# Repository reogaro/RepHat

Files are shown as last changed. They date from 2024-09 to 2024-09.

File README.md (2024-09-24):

# RepHat

"**R**epRap **E**xtension for **P**i"-**Hat**

Designed in Kicad. Open Source Hardware.

> [!CAUTION]
> This project is still in development and not ready for use!

A Raspberry Pi Hat for controlling stepper motors. Intended to be a [RAMPS](https://reprap.org/wiki/RAMPS_1.4) for the Raspberry Pi.

Built for use with LinuxCNC. See [here](https://github.com/reogaro/linuxcnc-pi4b-gpio) for some configuration examples.

## Features:

- 12-24 V Input Voltage
- 5V for Raspberry Pi with TI LMR51450 Switching Regulator
- Four Toshiba TB67S109AFTG Stepper Drivers
- Four endstop inputs with selectable voltages
- Input protection

## Current progress

[Schematic](output/schematic.pdf): Complete
[Routing](output/routing.pdf): Work in progress

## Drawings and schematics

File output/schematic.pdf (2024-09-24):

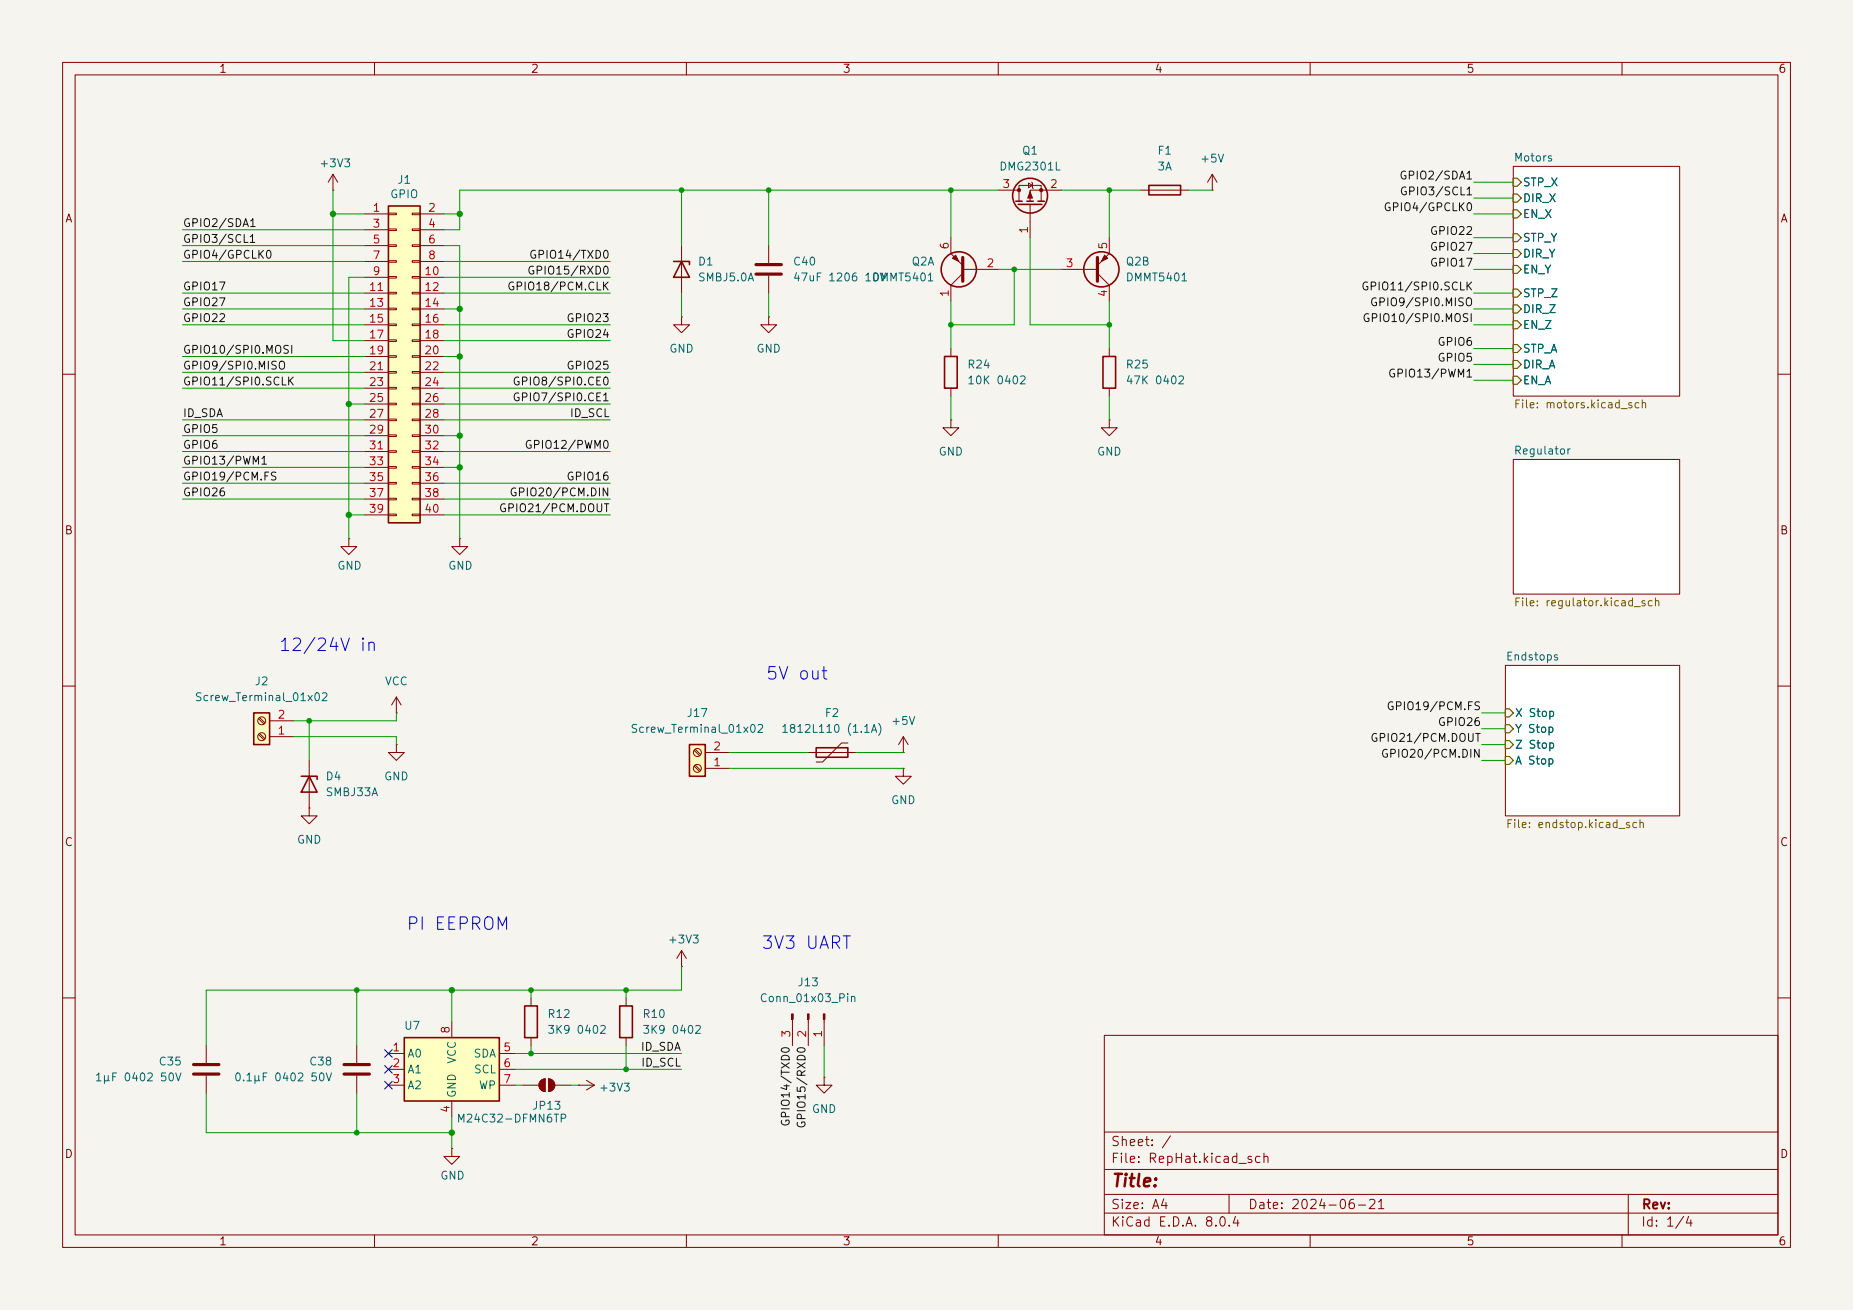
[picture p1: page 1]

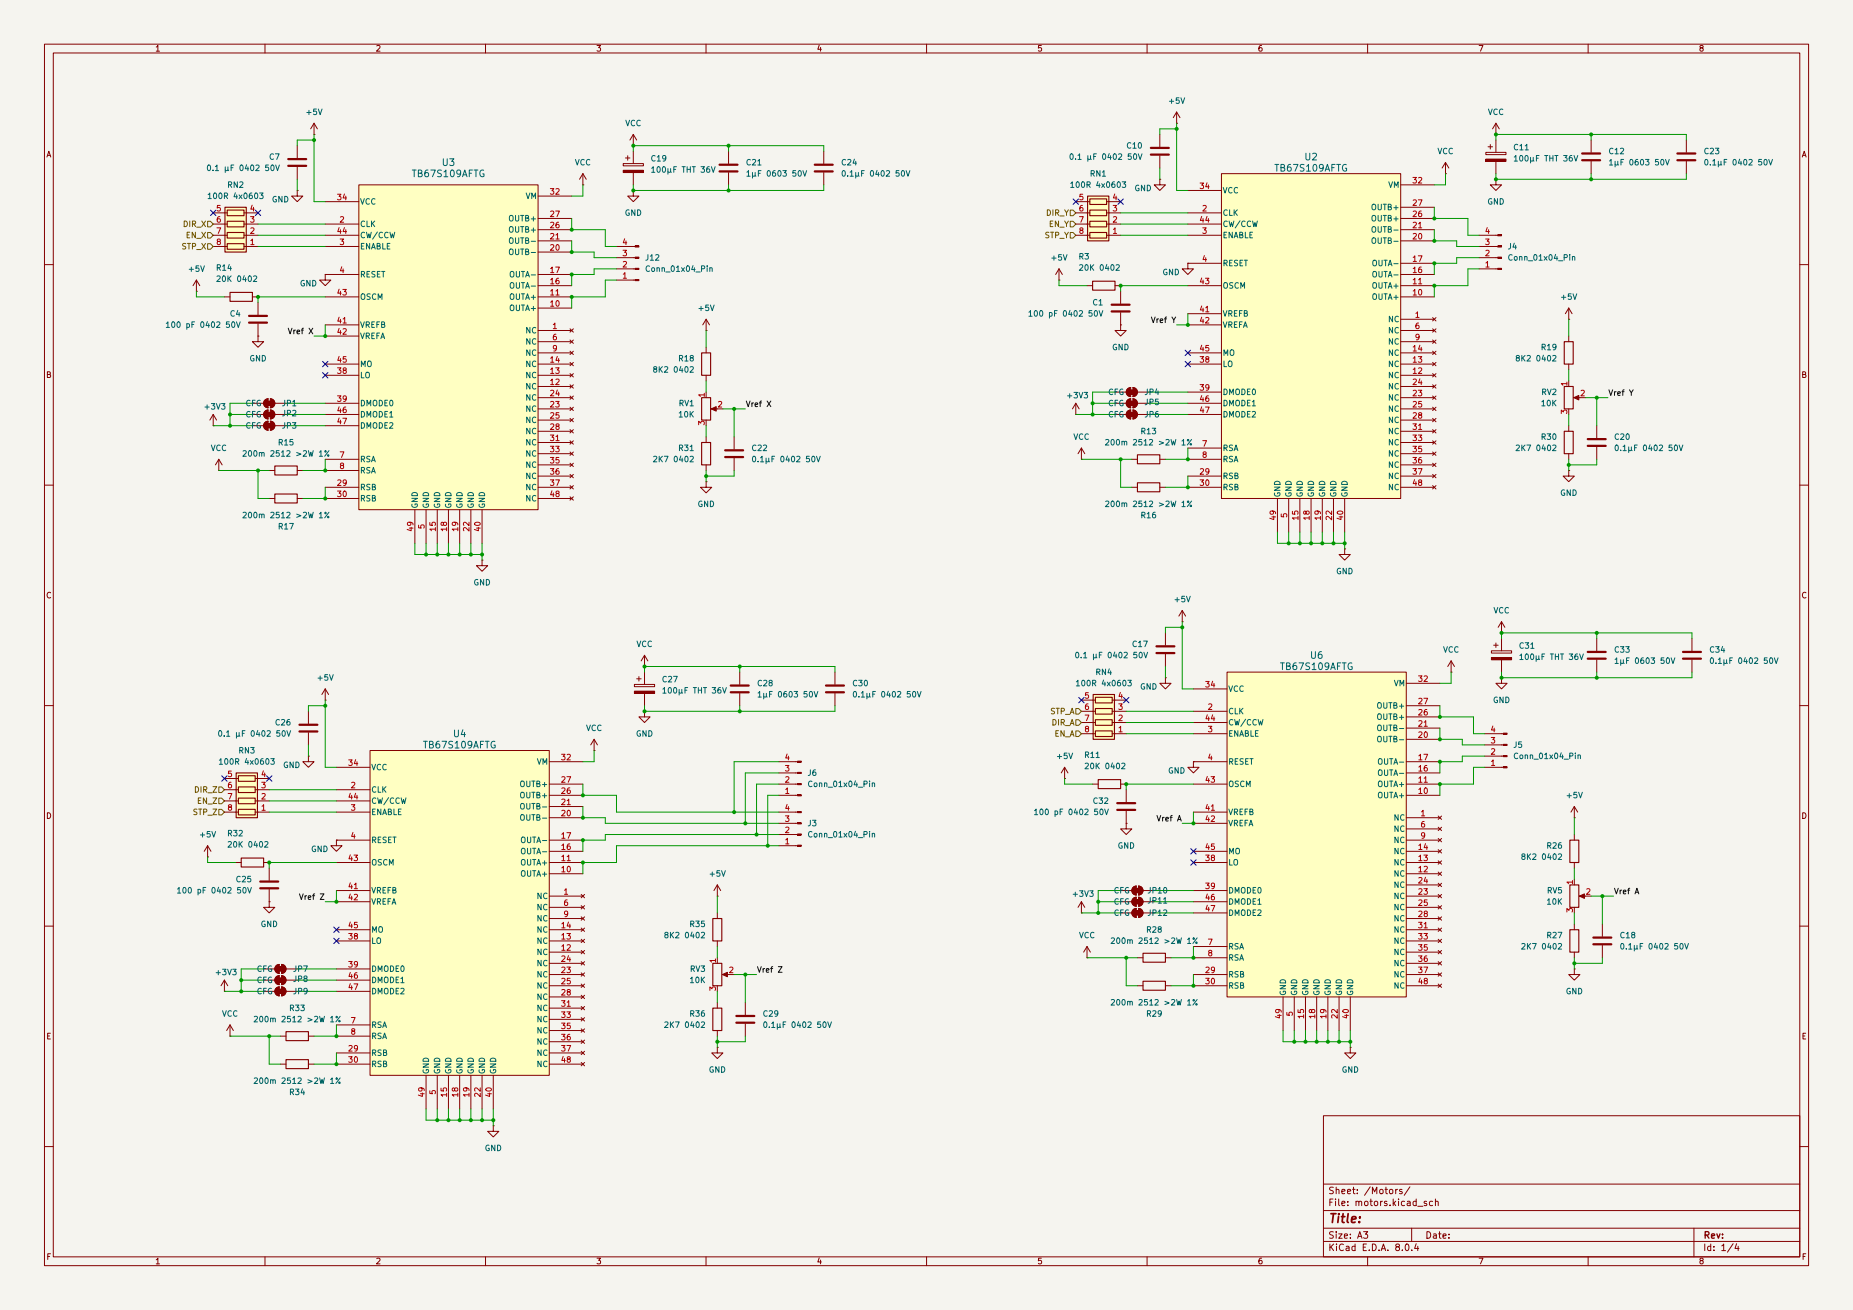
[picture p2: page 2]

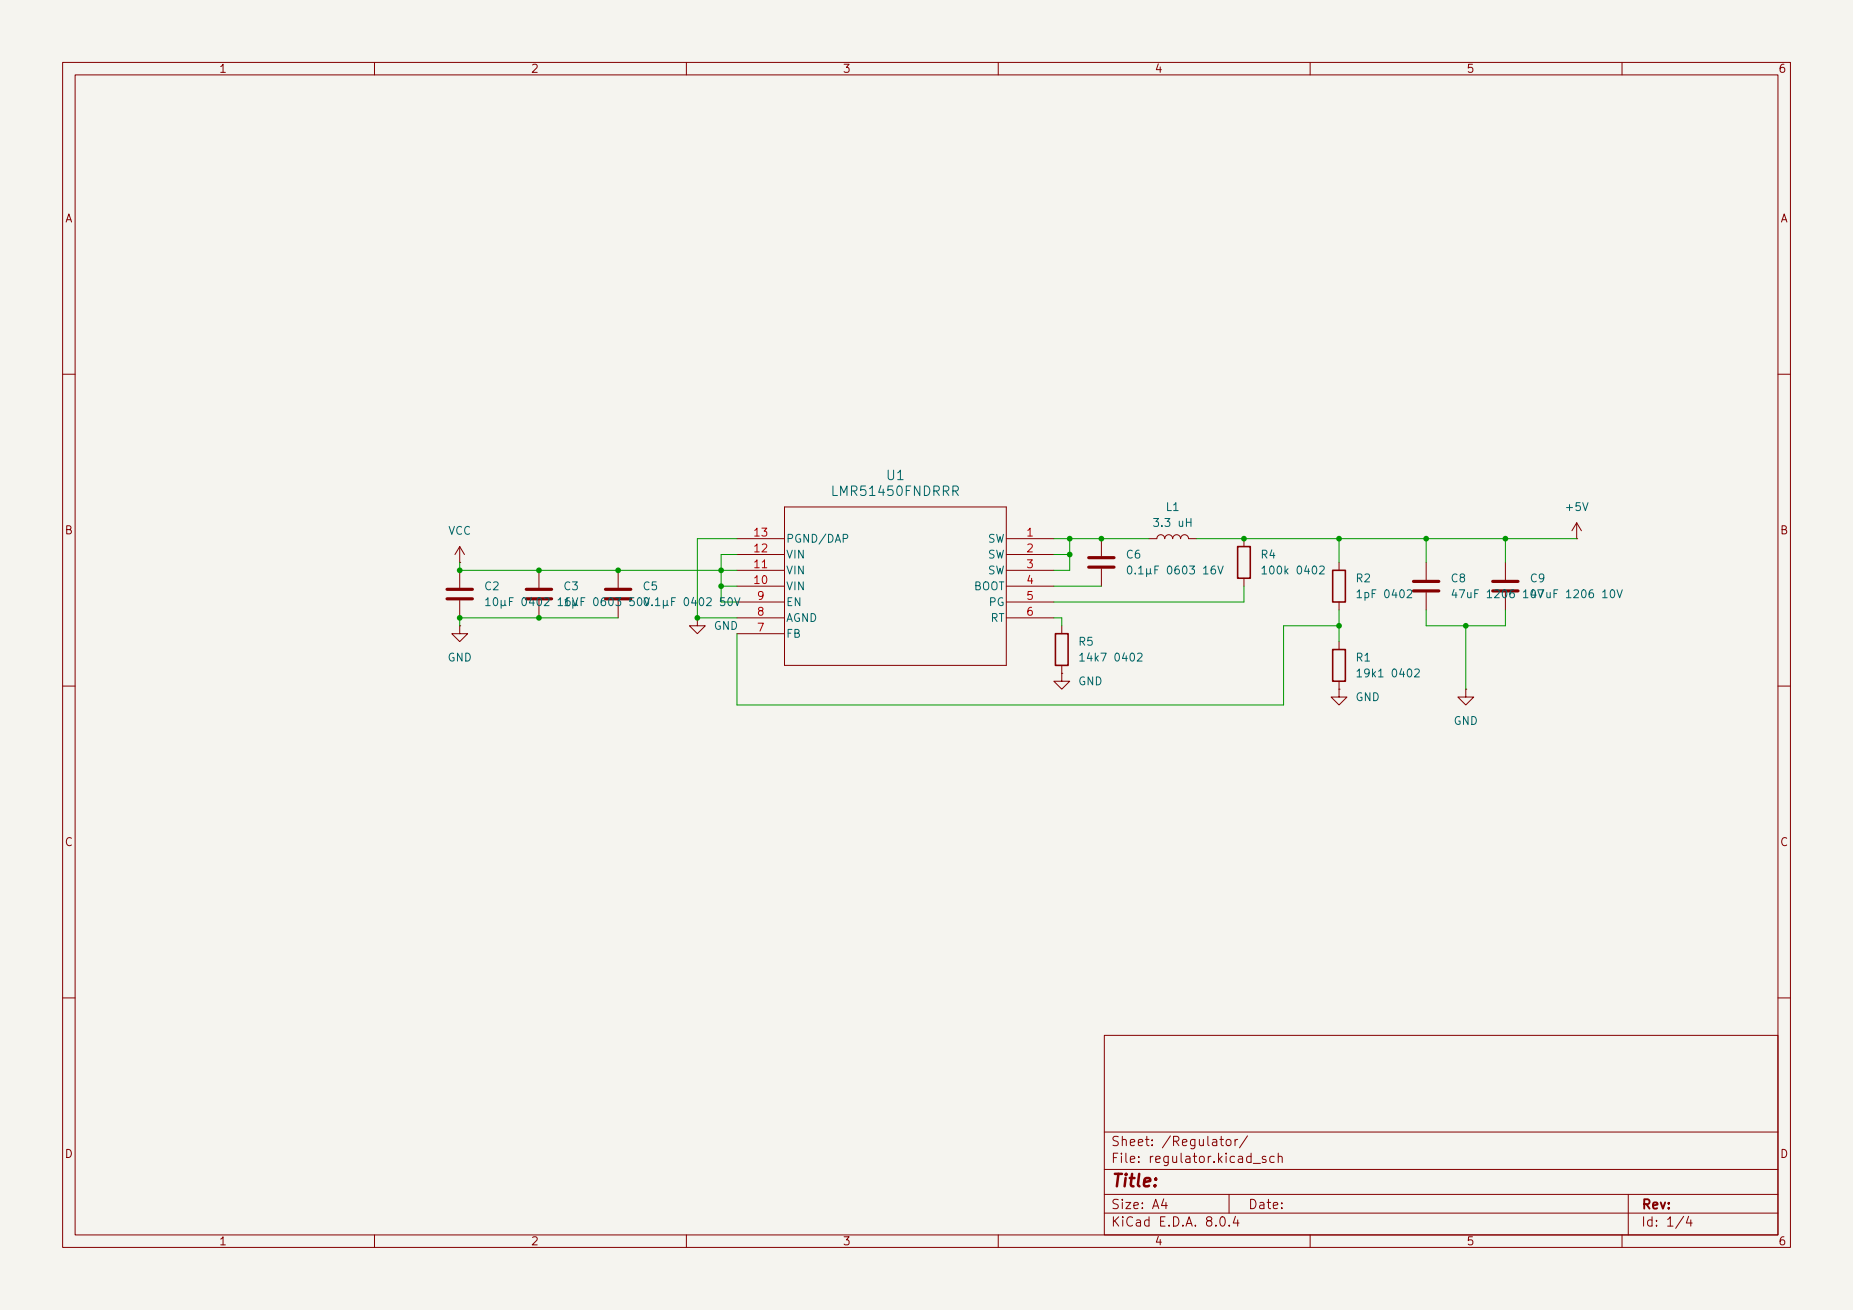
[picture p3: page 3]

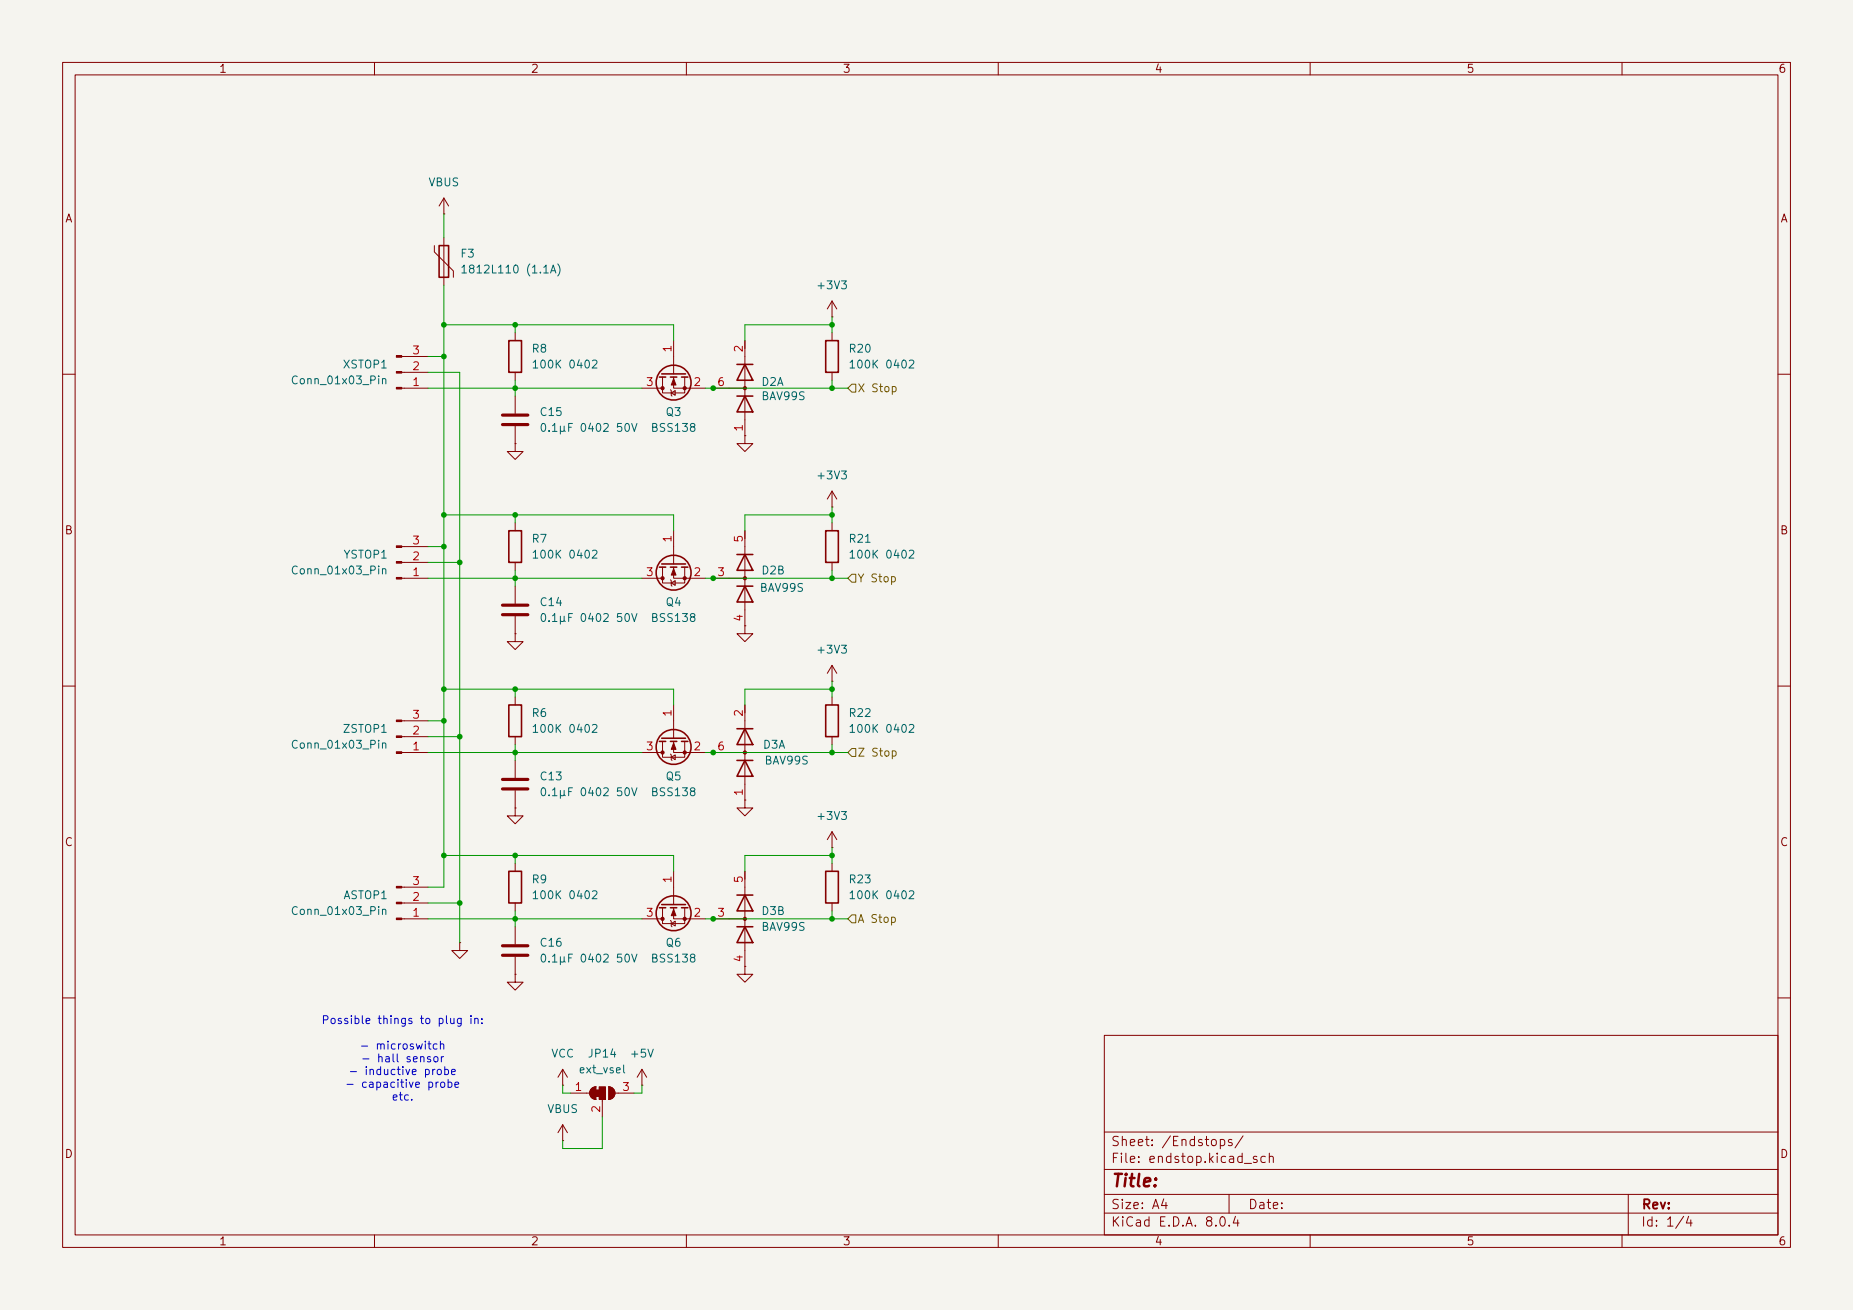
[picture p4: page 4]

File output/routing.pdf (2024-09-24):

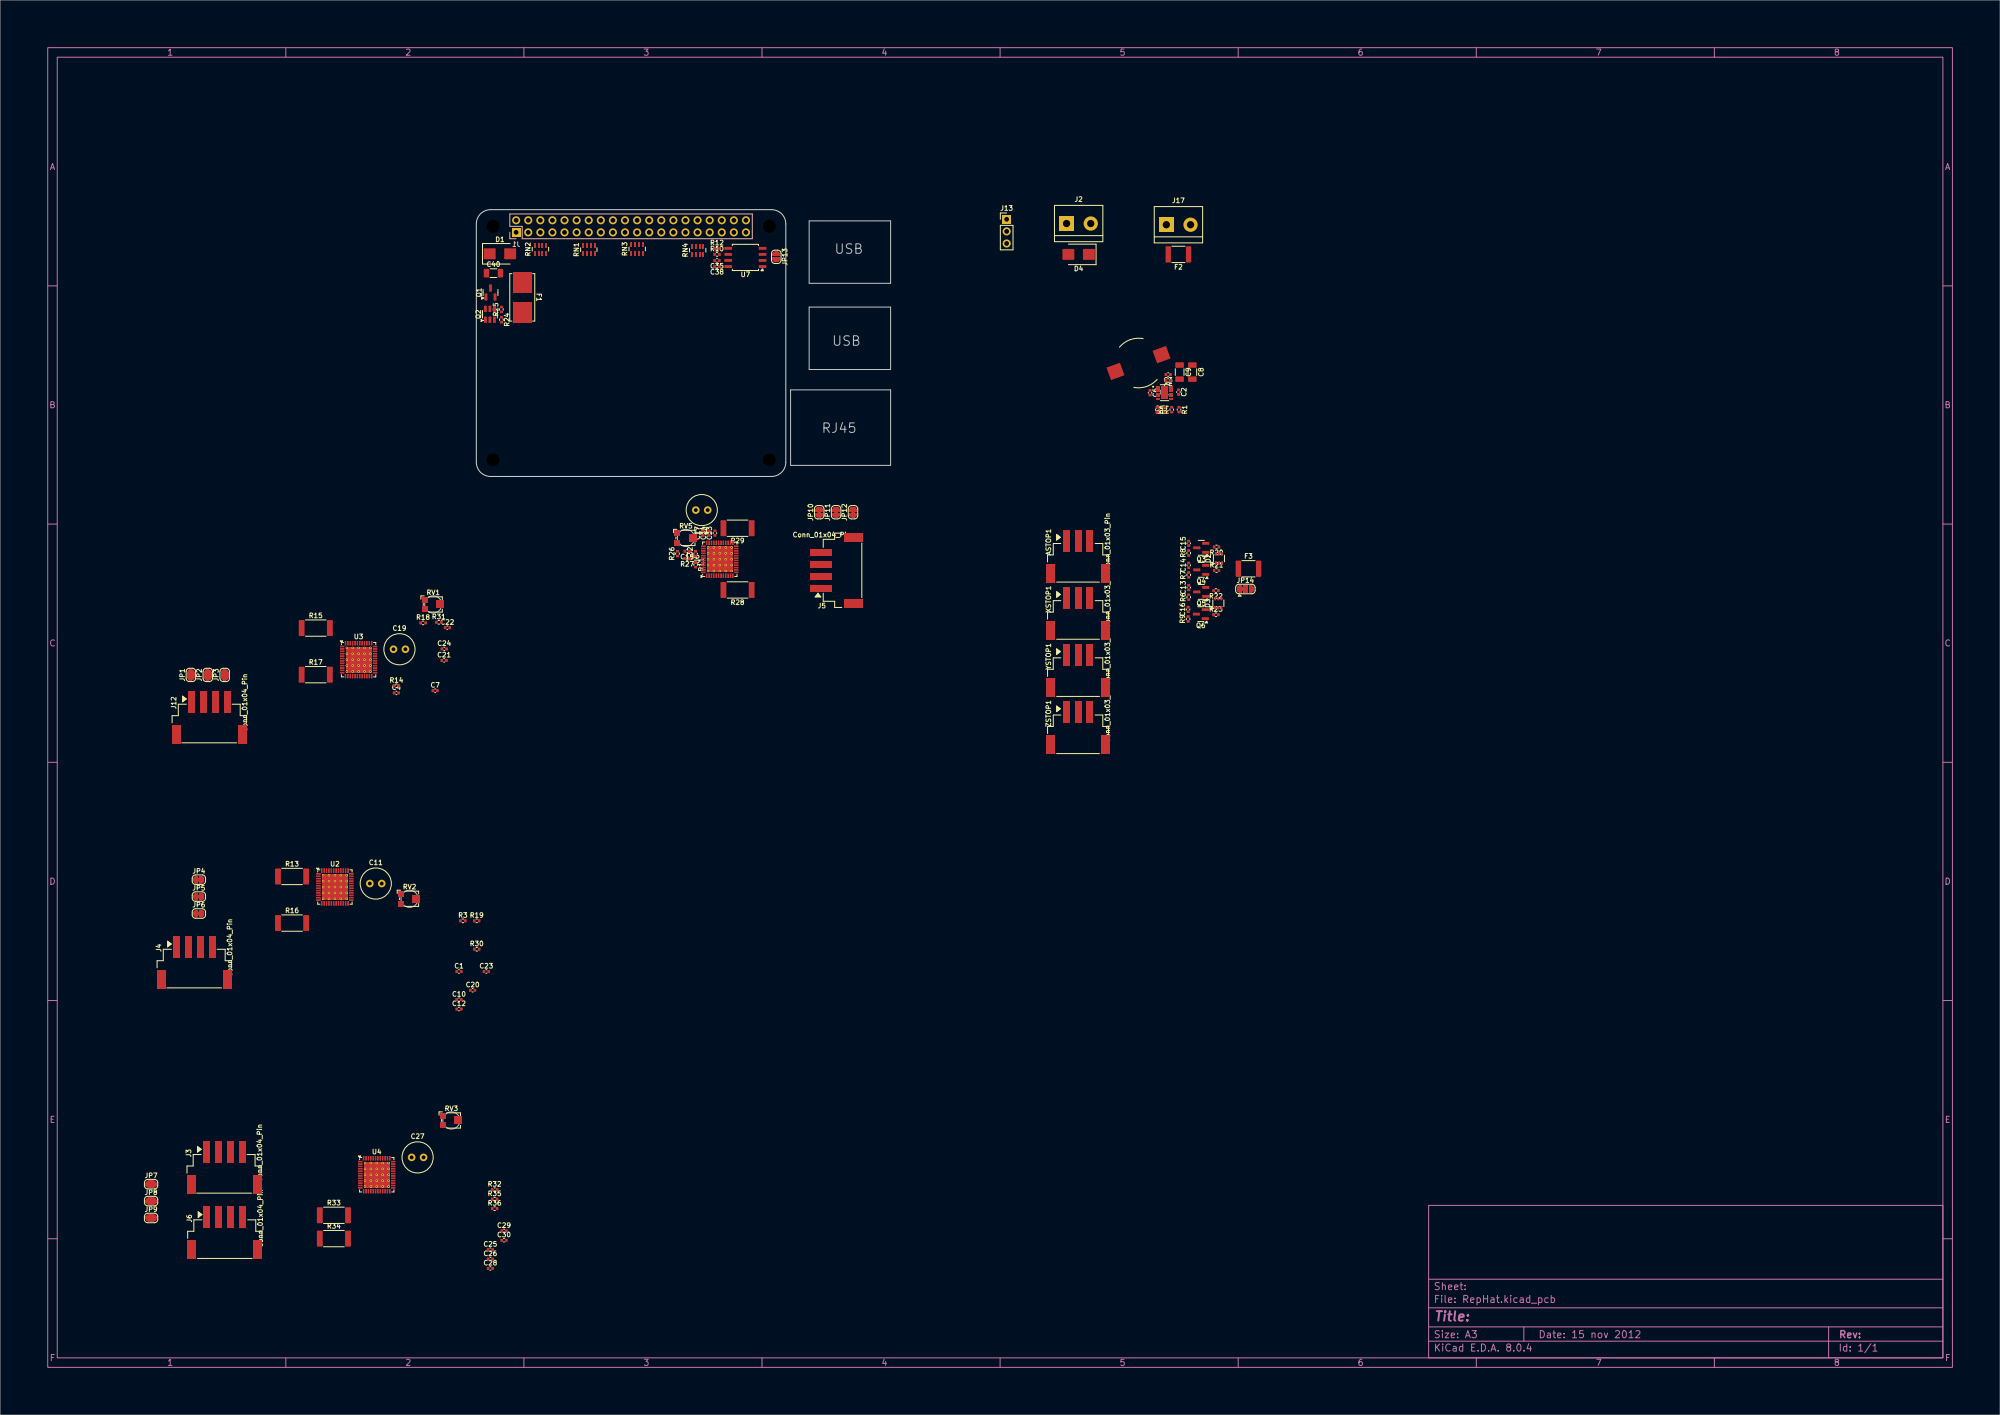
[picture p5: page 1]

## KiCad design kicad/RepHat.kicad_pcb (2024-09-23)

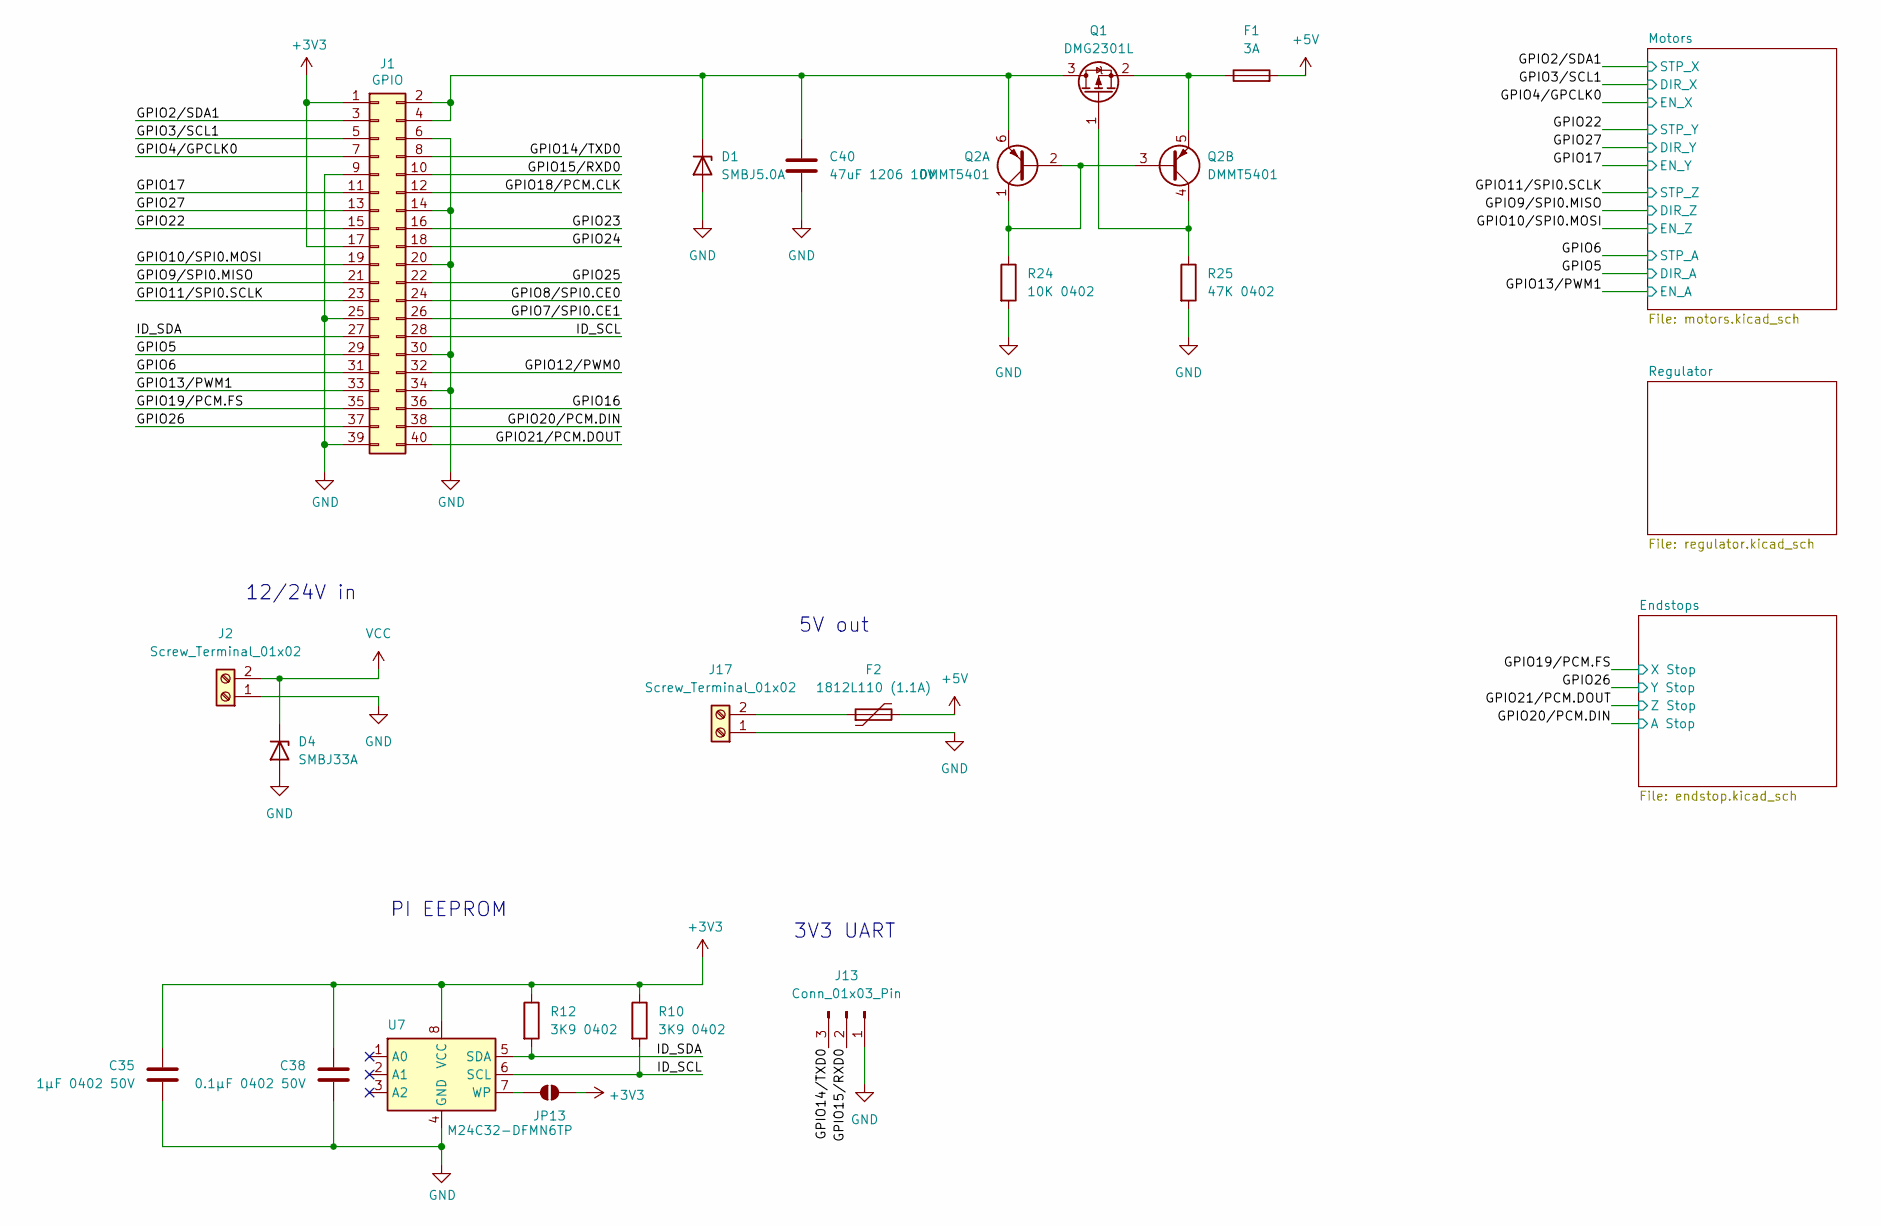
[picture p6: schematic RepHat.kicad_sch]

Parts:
C35: 1μF 0402 50V; C_0402_1005Metric
C38: 0.1μF 0402 50V; C_0402_1005Metric
C40: 47uF 1206 10V; C_1206_3216Metric
D1: SMBJ5.0A; D_SMB
D4: SMBJ33A; D_SMB
F1: 3A; Fuseholder_Littelfuse_Nano2_154x
F2: 1812L110 (1.1A); Fuse_1812_4532Metric
J1: GPIO; PinSocket_2x20_P2.54mm_Vertical
J2, J17: Screw_Terminal_01x02; TerminalBlock_bornier-2_P5.08mm
J13: Conn_01x03_Pin; PinHeader_1x03_P2.54mm_Vertical
JP13: ID_WP; SolderJumper-2_P1.3mm_Open_RoundedPad1.0x1.5mm
Q1: DMG2301L; SOT-23
Q2: DMMT5401; SOT-23-6
R10, R12: 3K9 0402; R_0402_1005Metric
R24: 10K 0402; R_0402_1005Metric
R25: 47K 0402; R_0402_1005Metric
U7: M24C32-DFMN6TP; SOIC-8_5.275x5.275mm_P1.27mm

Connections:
+3V3: C35.1, C38.1, J1.1, J1.17, JP13.2 (B), R10.1, R12.1, U7.8 (VCC); also elsewhere on the board
+5V: F1.2, F2.2; also elsewhere on the board
/GPIO2/SDA1: J1.3; also elsewhere on the board
/GPIO3/SCL1: J1.5; also elsewhere on the board
/GPIO4/GPCLK0: J1.7; also elsewhere on the board
/GPIO5: J1.29; also elsewhere on the board
/GPIO6: J1.31; also elsewhere on the board
/GPIO7/SPI0.CE1: J1.26
/GPIO8/SPI0.CE0: J1.24
/GPIO9/SPI0.MISO: J1.21; also elsewhere on the board
/GPIO10/SPI0.MOSI: J1.19; also elsewhere on the board
/GPIO11/SPI0.SCLK: J1.23; also elsewhere on the board
/GPIO12/PWM0: J1.32
/GPIO13/PWM1: J1.33; also elsewhere on the board
/GPIO14/TXD0: J1.8, J13.3
/GPIO15/RXD0: J1.10, J13.2
/GPIO16: J1.36
/GPIO17: J1.11; also elsewhere on the board
/GPIO18/PCM.CLK: J1.12
/GPIO19/PCM.FS: J1.35; also elsewhere on the board
/GPIO20/PCM.DIN: J1.38; also elsewhere on the board
/GPIO21/PCM.DOUT: J1.40; also elsewhere on the board
/GPIO22: J1.15; also elsewhere on the board
/GPIO23: J1.16
/GPIO24: J1.18
/GPIO25: J1.22
/GPIO26: J1.37; also elsewhere on the board
/GPIO27: J1.13; also elsewhere on the board
/ID_SCL: J1.28, R10.2, U7.6 (SCL)
/ID_SDA: J1.27, R12.2, U7.5 (SDA)
GND: C35.2, C38.2, C40.2, D1.2 (A), D4.2 (A), J1.6, J1.9, J1.14, J1.20, J1.25, J1.30, J1.34, J1.39, J2.1, J13.1, J17.1, R24.2, R25.2, U7.4 (GND); also elsewhere on the board
unnamed: C40.1, D1.1 (K), J1.2, J1.4, Q1.3 (D), Q2.6 (E1)
unnamed: F2.1, J17.2
unnamed: JP13.1 (A), U7.7 (WP)
unnamed: Q1.1 (G), Q2.4 (C2), R25.1
unnamed: F1.1, Q1.2 (S), Q2.5 (E2)
unnamed: Q2.1 (C1), Q2.2 (B1), Q2.3 (B2), R24.1
VCC: D4.1 (K), J2.2; also elsewhere on the board

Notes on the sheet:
12/24V in
PI EEPROM
5V out
3V3 UART

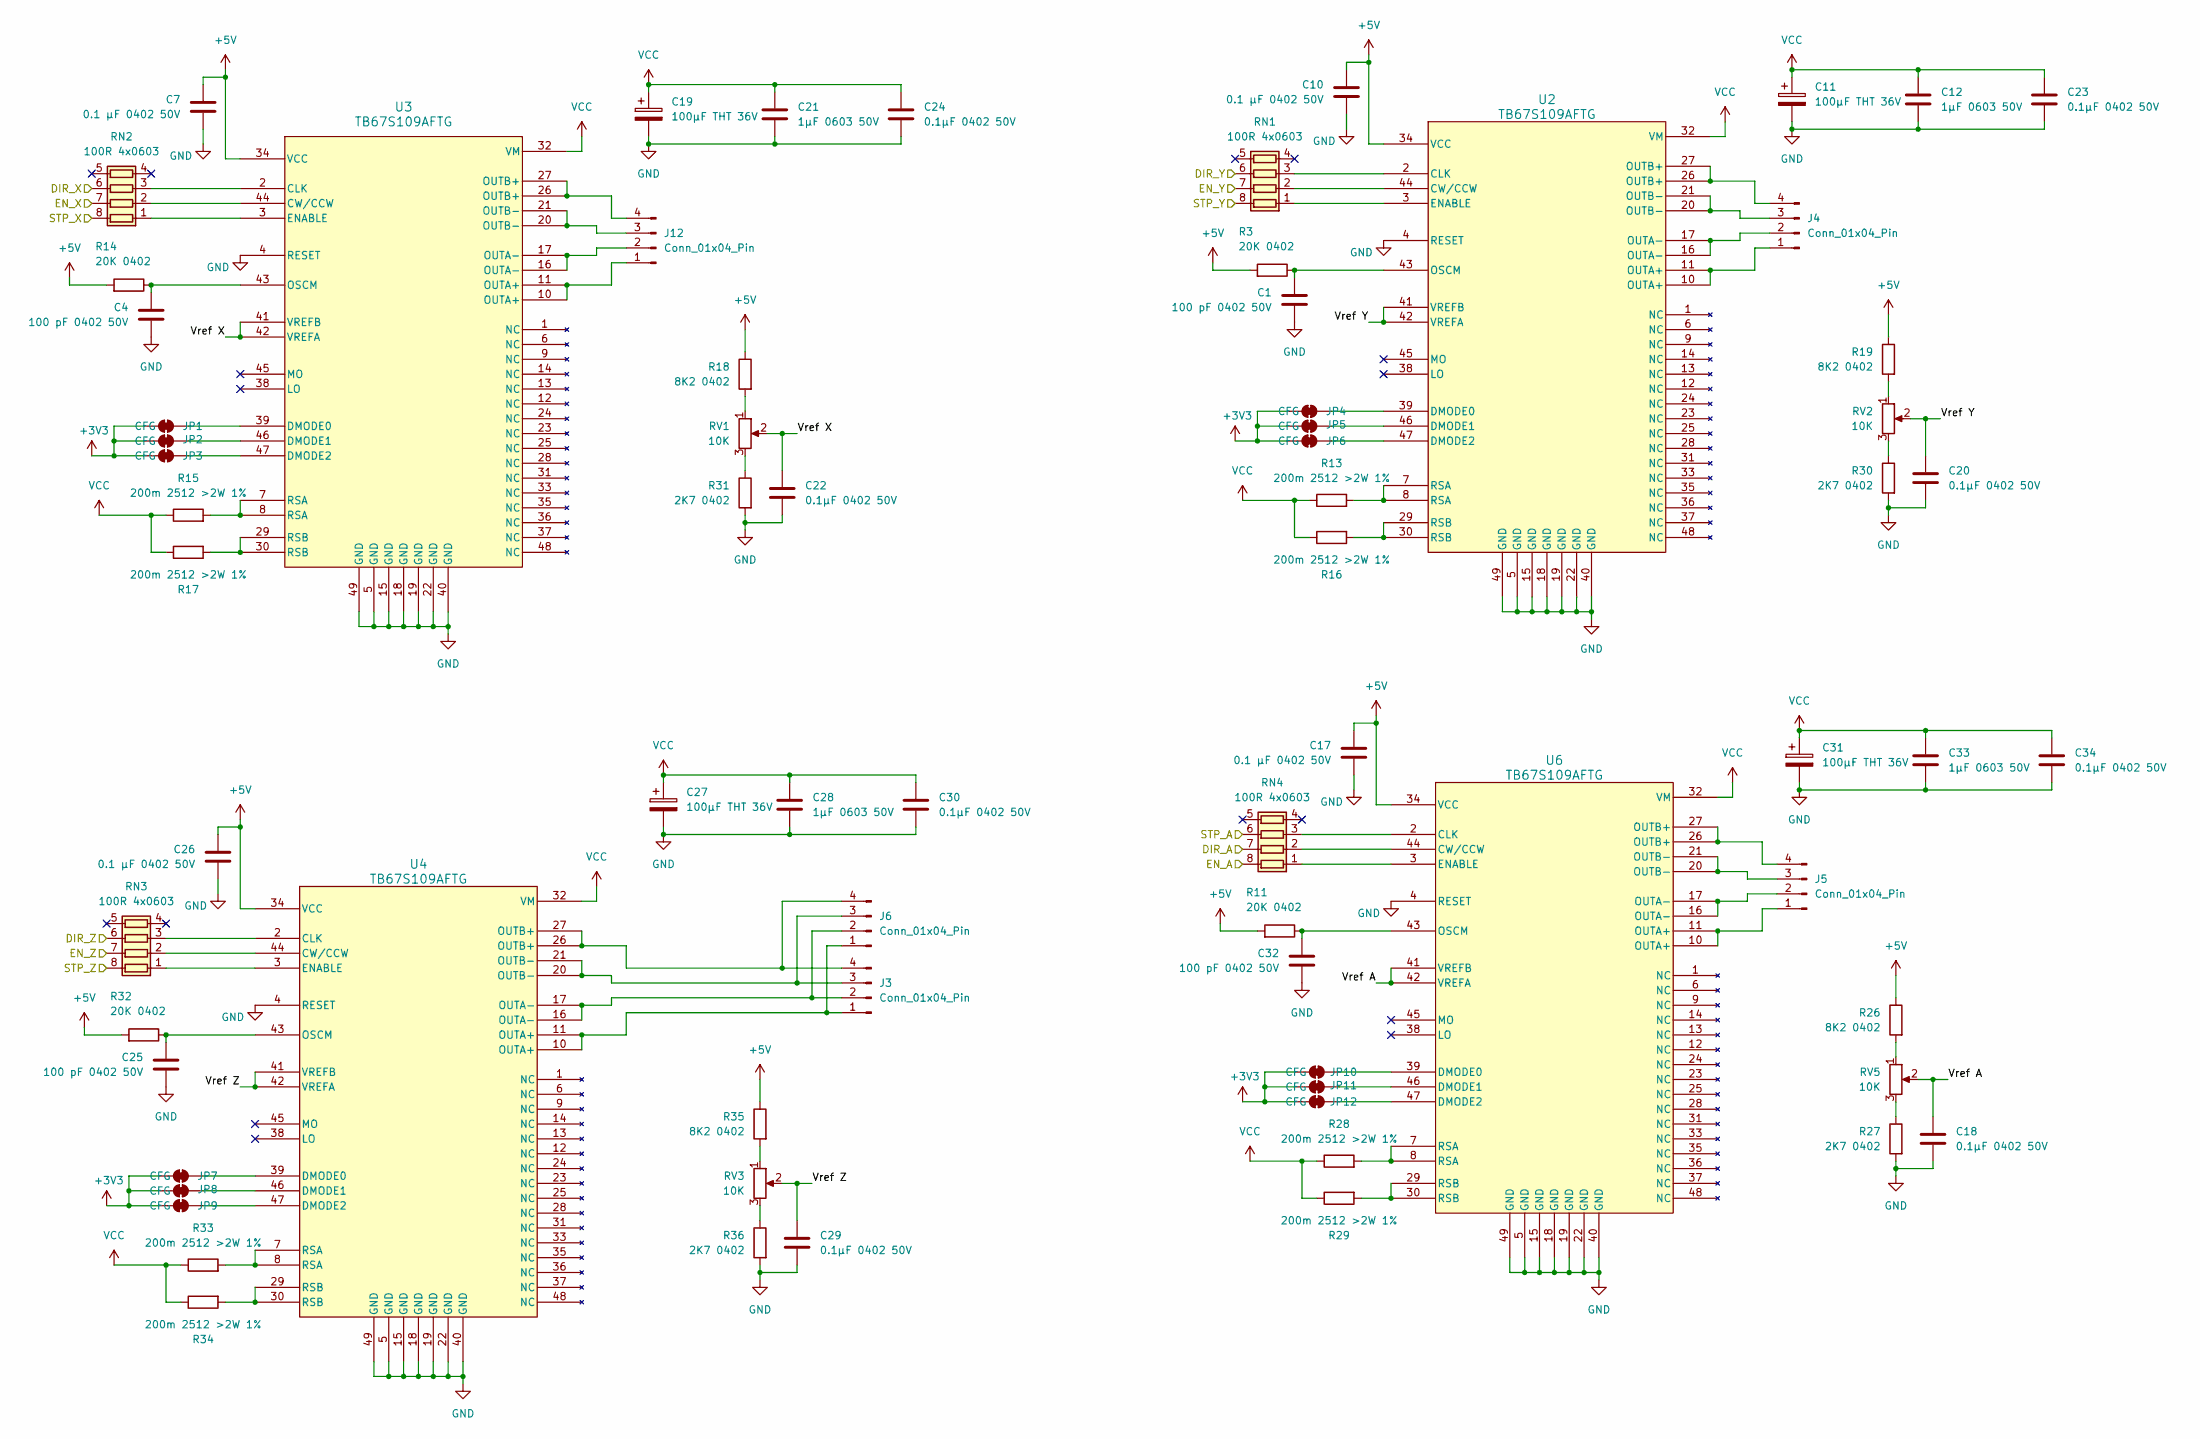
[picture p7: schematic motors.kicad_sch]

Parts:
C1, C4, C25, C32: 100 pF 0402 50V; C_0402_1005Metric
C7, C10, C17, C26: 0.1 μF 0402 50V; C_0402_1005Metric
C11, C19, C27, C31: 100μF THT 36V; C_Radial_D6.3mm_H11.0mm_P2.50mm
C12, C21, C28, C33: 1μF 0603 50V; C_0402_1005Metric
C18, C20, C22, C23, C24, C29, C30, C34: 0.1μF 0402 50V; C_0402_1005Metric
J3, J4, J5, J6, J12: Conn_01x04_Pin; S4B-XH-SM4-TB
JP1, JP2, JP3, JP4, JP5, JP6, JP7, JP8, JP9, JP10, JP11, JP12: CFG; SolderJumper-2_P1.3mm_Bridged_RoundedPad1.0x1.5mm
R3, R11, R14, R32: 20K 0402; R_0402_1005Metric
R13, R15, R16, R17, R28, R29, R33, R34: 200m 2512 >2W 1%; R_2512_6332Metric
R18, R19, R26, R35: 8K2 0402; R_0402_1005Metric
R27, R30, R31, R36: 2K7 0402; R_0402_1005Metric
RN1, RN2, RN3, RN4: 100R 4x0603; R_Array_Concave_4x0603
RV1, RV2, RV3, RV5: 10K; Potentiometer_Bourns_TC33X_Vertical
U2, U3, U4, U6: TB67S109AFTG; QFN-48-1EP_7x7mm_P0.5mm_EP5.45x5.45mm_ThermalVias

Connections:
+3V3: JP1.1 (A), JP2.1 (A), JP3.1 (A), JP4.1 (A), JP5.1 (A), JP6.1 (A), JP7.1 (A), JP8.1 (A), JP9.1 (A), JP10.1 (A), JP11.1 (A), JP12.1 (A); also elsewhere on the board
+5V: C7.1, C10.1, C17.1, C26.1, R3.2, R11.2, R14.2, R18.1, R19.1, R26.1, R32.2, R35.1, U2.34 (VCC), U3.34 (VCC), U4.34 (VCC), U6.34 (VCC); also elsewhere on the board
/GPIO2/SDA1: RN2.8 (R1.2); also elsewhere on the board
/GPIO3/SCL1: RN2.6 (R3.2); also elsewhere on the board
/GPIO4/GPCLK0: RN2.7 (R2.2); also elsewhere on the board
/GPIO5: RN4.7 (R2.2); also elsewhere on the board
/GPIO6: RN4.6 (R3.2); also elsewhere on the board
/GPIO9/SPI0.MISO: RN3.6 (R3.2); also elsewhere on the board
/GPIO10/SPI0.MOSI: RN3.7 (R2.2); also elsewhere on the board
/GPIO11/SPI0.SCLK: RN3.8 (R1.2); also elsewhere on the board
/GPIO13/PWM1: RN4.8 (R1.2); also elsewhere on the board
/GPIO17: RN1.7 (R2.2); also elsewhere on the board
/GPIO22: RN1.8 (R1.2); also elsewhere on the board
/GPIO27: RN1.6 (R3.2); also elsewhere on the board
/Motors/Vref A: C18.1, RV5.2, U6.41 (VREFB), U6.42 (VREFA)
/Motors/Vref X: C22.1, RV1.2, U3.41 (VREFB), U3.42 (VREFA)
/Motors/Vref Y: C20.1, RV2.2, U2.41 (VREFB), U2.42 (VREFA)
/Motors/Vref Z: C29.1, RV3.2, U4.41 (VREFB), U4.42 (VREFA)
GND: C1.2, C4.2, C7.2, C10.2, C11.2, C12.2, C17.2, C18.2, C19.2, C20.2, C21.2, C22.2, C23.2, C24.2, C25.2, C26.2, C27.2, C28.2, C29.2, C30.2, C31.2, C32.2, C33.2, C34.2, R27.2, R30.2, R31.2, R36.2, U2.4 (RESET), U2.5 (GND), U2.15 (GND), U2.18 (GND), U2.19 (GND), U2.22 (GND), U2.40 (GND), U2.49 (GND), U3.4 (RESET), U3.5 (GND), U3.15 (GND), U3.18 (GND), U3.19 (GND), U3.22 (GND), U3.40 (GND), U3.49 (GND), U4.4 (RESET), U4.5 (GND), U4.15 (GND), U4.18 (GND), U4.19 (GND), U4.22 (GND), U4.40 (GND), U4.49 (GND), U6.4 (RESET), U6.5 (GND), U6.15 (GND), U6.18 (GND), U6.19 (GND), U6.22 (GND), U6.40 (GND), U6.49 (GND); also elsewhere on the board
unnamed: J3.1, J6.1, U4.10 (OUTA+), U4.11 (OUTA+)
unnamed: J3.2, J6.2, U4.16 (OUTA-), U4.17 (OUTA-)
unnamed: J3.3, J6.3, U4.20 (OUTB-), U4.21 (OUTB-)
unnamed: J3.4, J6.4, U4.26 (OUTB+), U4.27 (OUTB+)
unnamed: J4.1, U2.10 (OUTA+), U2.11 (OUTA+)
unnamed: J4.2, U2.16 (OUTA-), U2.17 (OUTA-)
unnamed: J4.3, U2.20 (OUTB-), U2.21 (OUTB-)
unnamed: J4.4, U2.26 (OUTB+), U2.27 (OUTB+)
unnamed: J5.1, U6.10 (OUTA+), U6.11 (OUTA+)
unnamed: J5.2, U6.16 (OUTA-), U6.17 (OUTA-)
unnamed: J5.3, U6.20 (OUTB-), U6.21 (OUTB-)
unnamed: J5.4, U6.26 (OUTB+), U6.27 (OUTB+)
unnamed: J12.1, U3.10 (OUTA+), U3.11 (OUTA+)
unnamed: J12.2, U3.16 (OUTA-), U3.17 (OUTA-)
unnamed: J12.3, U3.20 (OUTB-), U3.21 (OUTB-)
unnamed: J12.4, U3.26 (OUTB+), U3.27 (OUTB+)
unnamed: JP1.2 (B), U3.39 (DMODE0)
unnamed: JP2.2 (B), U3.46 (DMODE1)
unnamed: JP3.2 (B), U3.47 (DMODE2)
unnamed: JP4.2 (B), U2.39 (DMODE0)
unnamed: JP5.2 (B), U2.46 (DMODE1)
unnamed: JP6.2 (B), U2.47 (DMODE2)
unnamed: JP7.2 (B), U4.39 (DMODE0)
unnamed: JP8.2 (B), U4.46 (DMODE1)
unnamed: JP9.2 (B), U4.47 (DMODE2)
unnamed: JP10.2 (B), U6.39 (DMODE0)
unnamed: JP11.2 (B), U6.46 (DMODE1)
unnamed: JP12.2 (B), U6.47 (DMODE2)
unnamed: R13.2, U2.7 (RSA), U2.8 (RSA)
unnamed: R15.2, U3.7 (RSA), U3.8 (RSA)
unnamed: R16.2, U2.29 (RSB), U2.30 (RSB)
unnamed: R17.2, U3.29 (RSB), U3.30 (RSB)
unnamed: R18.2, RV1.1
unnamed: R19.2, RV2.1
unnamed: R26.2, RV5.1
unnamed: R27.1, RV5.3
unnamed: R28.2, U6.7 (RSA), U6.8 (RSA)
unnamed: R29.2, U6.29 (RSB), U6.30 (RSB)
unnamed: R30.1, RV2.3
unnamed: R31.1, RV1.3
unnamed: R33.2, U4.7 (RSA), U4.8 (RSA)
unnamed: R34.2, U4.29 (RSB), U4.30 (RSB)
unnamed: R35.2, RV3.1
unnamed: R36.1, RV3.3
unnamed: RN1.1 (R1.1), U2.3 (ENABLE)
unnamed: RN1.2 (R2.1), U2.44 (CW/CCW)
unnamed: RN1.3 (R3.1), U2.2 (CLK)
unnamed: RN2.1 (R1.1), U3.3 (ENABLE)
unnamed: RN2.2 (R2.1), U3.44 (CW/CCW)
unnamed: RN2.3 (R3.1), U3.2 (CLK)
unnamed: RN3.1 (R1.1), U4.3 (ENABLE)
unnamed: RN3.2 (R2.1), U4.44 (CW/CCW)
unnamed: RN3.3 (R3.1), U4.2 (CLK)
unnamed: RN4.1 (R1.1), U6.3 (ENABLE)
unnamed: RN4.2 (R2.1), U6.44 (CW/CCW)
unnamed: RN4.3 (R3.1), U6.2 (CLK)
unnamed: C1.1, R3.1, U2.43 (OSCM)
unnamed: C4.1, R14.1, U3.43 (OSCM)
unnamed: C25.1, R32.1, U4.43 (OSCM)
unnamed: C32.1, R11.1, U6.43 (OSCM)
VCC: C11.1, C12.1, C19.1, C21.1, C23.1, C24.1, C27.1, C28.1, C30.1, C31.1, C33.1, C34.1, R13.1, R15.1, R16.1, R17.1, R28.1, R29.1, R33.1, R34.1, U2.32 (VM), U3.32 (VM), U4.32 (VM), U6.32 (VM); also elsewhere on the board

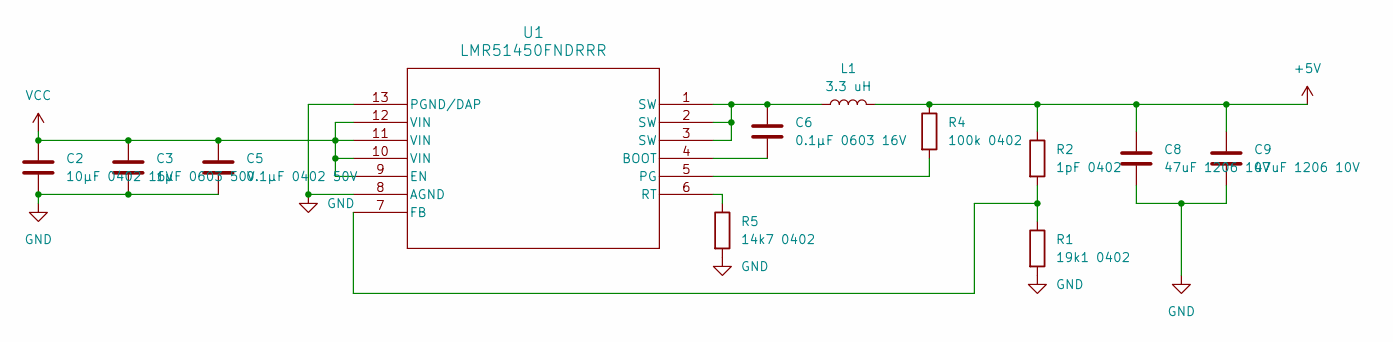
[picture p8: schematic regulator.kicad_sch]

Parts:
C2: 10μF 0402 16V; C_0402_1005Metric
C3: 1μF 0603 50V; C_0402_1005Metric
C5: 0.1μF 0402 50V; C_0402_1005Metric
C6: 0.1μF 0603 16V; C_0402_1005Metric
C8, C9: 47uF 1206 10V; C_1206_3216Metric
L1: 3.3 uH; L_Wuerth_WE-PD4-Typ-L
R1: 19k1 0402; R_0402_1005Metric
R2: 1pF 0402; R_0402_1005Metric
R4: 100k 0402; R_0402_1005Metric
R5: 14k7 0402; R_0402_1005Metric
U1: LMR51450FNDRRR; WSON_SDRRR_TEX

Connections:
+5V: C8.1, C9.1, L1.1, R2.1, R4.1; also elsewhere on the board
GND: C2.2, C3.2, C5.2, C8.2, C9.2, R1.2, R5.2, U1.8 (AGND), U1.13 (PGND/DAP); also elsewhere on the board
unnamed: C6.1, L1.2, U1.1 (SW), U1.2 (SW), U1.3 (SW)
unnamed: C6.2, U1.4 (BOOT)
unnamed: R1.1, R2.2, U1.7 (FB)
unnamed: R4.2, U1.5 (PG)
unnamed: R5.1, U1.6 (RT)
VCC: C2.1, C3.1, C5.1, U1.9 (EN), U1.10 (VIN), U1.11 (VIN), U1.12 (VIN); also elsewhere on the board

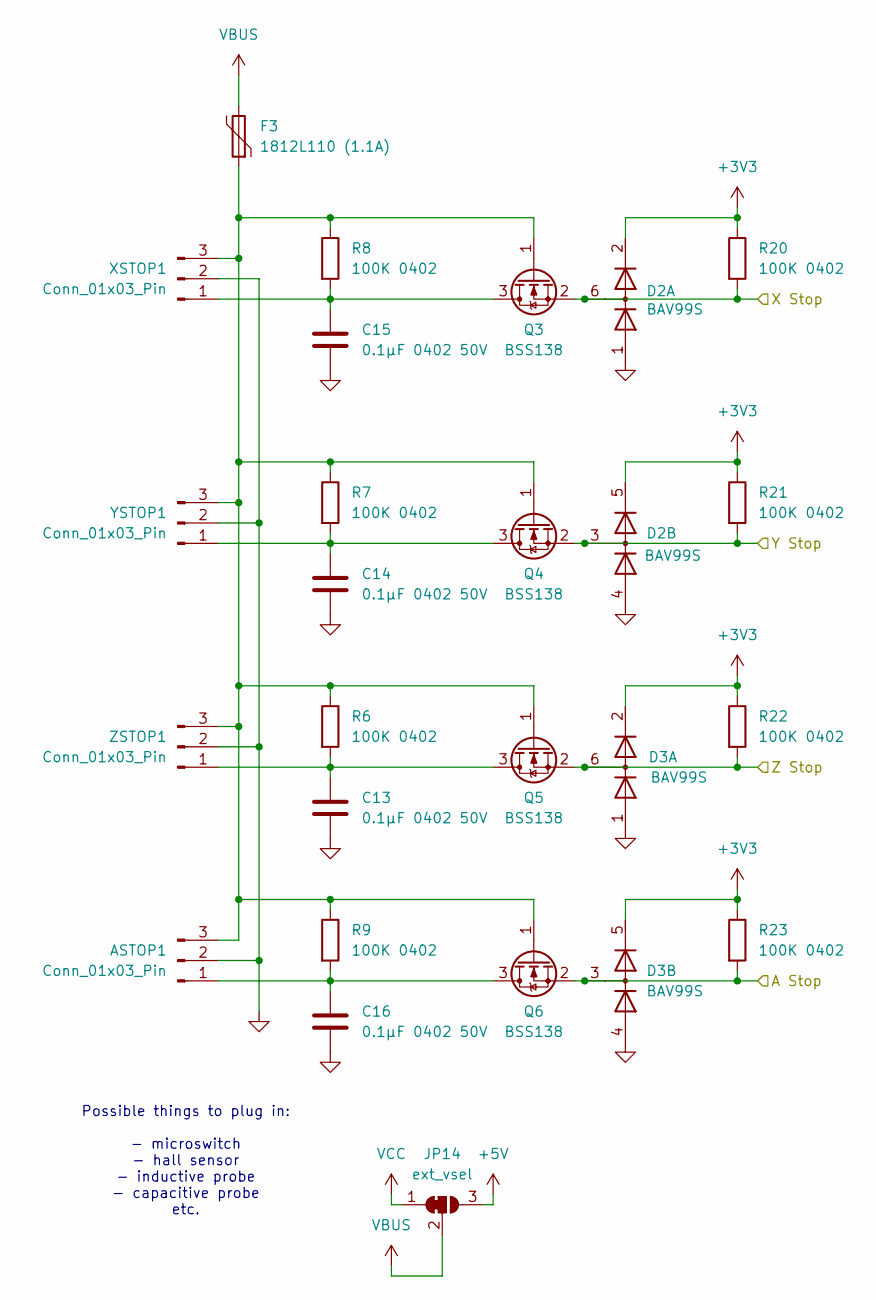
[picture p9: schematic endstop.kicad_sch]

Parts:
ASTOP1: Conn_01x03_Pin; S3B-XH-SM4-TB
C13, C14, C15, C16: 0.1μF 0402 50V; C_0402_1005Metric
D2, D3: BAV99S; SOT-363_SC-70-6
F3: 1812L110 (1.1A); Fuse_1812_4532Metric
JP14: ext_vsel; SolderJumper-3_P1.3mm_Bridged12_RoundedPad1.0x1.5mm
Q3, Q4, Q5, Q6: BSS138; SOT-23
R6, R7, R8, R9, R20, R21, R22, R23: 100K 0402; R_0402_1005Metric
XSTOP1: Conn_01x03_Pin; S3B-XH-SM4-TB
YSTOP1: Conn_01x03_Pin; S3B-XH-SM4-TB
ZSTOP1: Conn_01x03_Pin; S3B-XH-SM4-TB

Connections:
+3V3: D2.2 (K2), D2.5 (K4), D3.2 (K2), D3.5 (K4), R20.1, R21.1, R22.1, R23.1; also elsewhere on the board
+5V: JP14.3 (B); also elsewhere on the board
/GPIO19/PCM.FS: D2.6 (K3A4), Q3.2 (S), R20.2; also elsewhere on the board
/GPIO20/PCM.DIN: D3.3 (K1A2), Q6.2 (S), R23.2; also elsewhere on the board
/GPIO21/PCM.DOUT: D3.6 (K3A4), Q5.2 (S), R22.2; also elsewhere on the board
/GPIO26: D2.3 (K1A2), Q4.2 (S), R21.2; also elsewhere on the board
GND: ASTOP1.2, C13.2, C14.2, C15.2, C16.2, D2.1 (A1), D2.4 (A3), D3.1 (A1), D3.4 (A3), XSTOP1.2, YSTOP1.2, ZSTOP1.2; also elsewhere on the board
unnamed: ASTOP1.1, C16.1, Q6.3 (D), R9.2
unnamed: ASTOP1.3, F3.1, Q3.1 (G), Q4.1 (G), Q5.1 (G), Q6.1 (G), R6.1, R7.1, R8.1, R9.1, XSTOP1.3, YSTOP1.3, ZSTOP1.3
unnamed: C15.1, Q3.3 (D), R8.2, XSTOP1.1
unnamed: C14.1, Q4.3 (D), R7.2, YSTOP1.1
unnamed: C13.1, Q5.3 (D), R6.2, ZSTOP1.1
VBUS: F3.2, JP14.2 (C)
VCC: JP14.1 (A); also elsewhere on the board

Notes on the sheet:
Possible things to plug in: - microswitch - hall sensor - inductive probe - capacitive probe etc.

Board: 2 copper layers, 132 parts (1 on the bottom side), 105 nets, no tracks yet.

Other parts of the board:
MH1, MH2, MH3, MH4: MountingHole_2.7mm_M2.5

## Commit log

2024-06-01 initial fixes
    [RepHat.kicad_pcb]
2024-06-02 Endstops buffered & regulator 1MHz
    [RepHat.kicad_sch, endstop.kicad_sch, regulator.kicad_sch]
2024-06-04 TMC2209 progress
    [motors.kicad_sch]
2024-06-04 reorganized files
    [RepHat.kicad_pcb, RepHat.kicad_sch, endstop.kicad_sch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]
2024-06-05 Miniaturizing the stepper drivers. They're still too big
    [RepHat.kicad_pcb, RepHat.kicad_sch, endstop.kicad_sch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]
2024-06-11 TMC2209->TMC2100, endstop protection optimization
    [RepHat.kicad_sch, endstop.kicad_sch, motors.kicad_sch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]
2024-06-12 DRV8825 schematic
    [RepHat.kicad_sch, endstop.kicad_sch, motors.kicad_sch]
2024-06-12 PCB redo
    [RepHat.kicad_pcb, endstop.kicad_sch, motors.kicad_sch]
2024-06-21 schematic candidate 0
    [RepHat.kicad_pcb, RepHat.kicad_sch, endstop.kicad_sch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]
2024-06-28 Toshiba TB67S109A stepper driver
    [motors.kicad_sch]
2024-07-02 new level shifter: bss138 transistors
    [RepHat.kicad_sch, endstop.kicad_sch, regulator.kicad_sch]
2024-07-02 TB67S109A schematic wired
    [motors.kicad_sch]
2024-09-10 schematic finished
    [RepHat.kicad_pcb, RepHat.kicad_sch, endstop.kicad_sch]
2024-09-23 layout progress
    [RepHat.kicad_pcb, RepHat.kicad_sch, endstop.kicad_sch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]
